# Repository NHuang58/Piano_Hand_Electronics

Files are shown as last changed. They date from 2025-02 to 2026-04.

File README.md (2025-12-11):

# Piano-Hand-API
API using Music 21 and MIDI to convert midi files and piano notes to coordinates for a piano hand.

The KiCAD files have a full PCB design for the barrel jack, LM2896, motor servers, stepper motor driver, and microphone. This includes the Gerber files, drill files, and bill of materials. It also includes the libraries for the symbols and footprints used in this project.

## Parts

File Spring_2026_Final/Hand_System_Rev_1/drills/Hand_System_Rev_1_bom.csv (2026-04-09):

Reference | Qty | Value | DNP | Exclude from BOM | Exclude from Board | Footprint | Datasheet
C1 | 1 | 22u |  |  |  | Capacitor_SMD:C_0805_2012Metric | ~
C2 | 1 | 100 μF |  |  |  | Capacitor_SMD:C_0805_2012Metric | ~
C3,C4 | 2 | 10uF |  |  |  | Capacitor_SMD:C_0805_2012Metric | ~
H1,H2,H3,H4 | 4 | MountingHole |  | Excluded from BOM |  | MountingHole:MountingHole_4.3mm_M4 | ~
J1 | 1 | Barrel_Jack |  |  |  | Connector_BarrelJack:BarrelJack_SwitchcraftConxall_RAPC10U_Horizontal | https://www.sameskydevices.com/product/resource/pj-007.pdf
M1,M2,M3,M4,M5,M6,M8,M9,M10,M11 | 10 | Motor_Servo |  |  |  | Connector_PinHeader_2.54mm:PinHeader_1x03_P2.54mm_Vertical | ~
M7 | 1 | Stepper_Motor |  |  |  | Connector_PinHeader_2.54mm:PinHeader_1x04_P2.54mm_Vertical | ~
Q1,Q3 | 2 | IRLZ44N |  |  |  | Package_TO_SOT_THT:TO-220-3_Vertical | https://www.infineon.com/assets/row/public/documents/24/49/infineon-irlz44n-datasheet-en.pdf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
R1,R14,R28,R35 | 4 | 10k |  |  |  | Resistor_SMD:R_0805_2012Metric | ~
R2,R15 | 2 | 100 |  |  |  | Resistor_SMD:R_0805_2012Metric | ~
R3,R4,R5,R6,R7,R8,R9,R10,R11,R12 | 10 | 1K |  |  |  | Resistor_SMD:R_0805_2012Metric | ~
R13,R16 | 2 | 1k |  |  |  | Resistor_SMD:R_0805_2012Metric | ~
R23,R24,R25,R26,R27,R36,R37,R38,R39,R40 | 10 | 220 |  |  |  | Resistor_SMD:R_0805_2012Metric | ~
U1 | 1 | ESP32-DEVKITC-32UE |  |  |  | DEVKIT_V1_ESP32-WROOM-32:MODULE_DEVKIT_V1_ESP32-WROOM-32
U2,U5,U6 | 3 | LM2596 |  |  |  | PCB_Components:LM2596 | https://www.amazon.com/Seloky-Converter-Adjustable-Electronic-Stabilizer/dp/B0DBVYP91F
U3 | 1 | A4988_Stepper_Motor_Driver |  |  |  | Module:Pololu_Breakout-16_15.2x20.3mm | https://www.pololu.com/product/2980/pictures
U4 | 1 | ~ |  |  |  | Connector_PinHeader_2.54mm:PinHeader_1x04_P2.54mm_Vertical
U7,U8 | 2 | PCA9685PW |  |  |  | Package_SO:TSSOP-28_4.4x9.7mm_P0.65mm | http://www.nxp.com/docs/en/data-sheet/PCA9685.pdf

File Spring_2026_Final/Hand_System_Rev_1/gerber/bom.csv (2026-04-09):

Reference | Qty | Value | DNP | Exclude from BOM | Exclude from Board | Footprint | Datasheet
C1 | 1 | 22u |  |  |  | Capacitor_SMD:C_0805_2012Metric | https://www.mouser.com/ProductDetail/Murata-Electronics/GXT21BR61C226ME13L?qs=d0WKAl%252BL4Kb74FO4906dbA%3D%3D
C2 | 1 | 100 uF |  |  |  | Capacitor_SMD:C_1206_3216Metric | https://www.mouser.com/ProductDetail/Murata-Electronics/GRM31CR61A107MEA8K?qs=hd1VzrDQEGiKPwOlEhCnYw%3D%3D
C3,C4 | 2 | 10uF |  |  |  | Capacitor_SMD:C_0805_2012Metric | https://www.digikey.com/en/products/detail/yageo/CC0805KRX5R7BB106/7164386
H1,H2,H3,H4 | 4 | MountingHole |  | Excluded from BOM |  | MountingHole:MountingHole_4.3mm_M4 | ~
J1 | 1 | Barrel_Jack |  |  |  | Connector_BarrelJack:BarrelJack_SwitchcraftConxall_RAPC10U_Horizontal | https://www.sameskydevices.com/product/resource/pj-007.pdf
M1,M2,M3,M4,M5,M6,M8,M9,M10,M11 | 10 | Motor_Servo |  |  |  | Connector_PinHeader_2.54mm:PinHeader_1x03_P2.54mm_Vertical | ~
M7 | 1 | Stepper_Motor |  |  |  | Connector_PinHeader_2.54mm:PinHeader_1x04_P2.54mm_Vertical | ~
Q1,Q3 | 2 | IRLZ44N |  |  |  | Package_TO_SOT_THT:TO-220-3_Vertical | https://www.infineon.com/assets/row/public/documents/24/49/infineon-irlz44n-datasheet-en.pdf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
R1,R14,R28,R35 | 4 | 10k |  |  |  | Resistor_SMD:R_0805_2012Metric | https://www.digikey.com/en/products/detail/yageo/RC0805FR-0710KL/727535
R2,R15 | 2 | 100 |  |  |  | Resistor_SMD:R_0805_2012Metric | https://www.digikey.com/en/products/detail/yageo/RC0402FR-07100RL/726527
R3,R4,R5,R6,R7,R8,R9,R10,R11,R12 | 10 | 1K |  |  |  | Resistor_SMD:R_0805_2012Metric | https://www.digikey.com/en/products/detail/vishay-dale/CRCW08051K00FKEA/1175637
R13,R16 | 2 | 1k |  |  |  | Resistor_SMD:R_0805_2012Metric | https://www.digikey.com/en/products/detail/vishay-dale/CRCW08051K00FKEA/1175637
R23,R24,R25,R26,R27,R36,R37,R38,R39,R40 | 10 | 220 |  |  |  | Resistor_SMD:R_0805_2012Metric | https://www.digikey.com/en/products/detail/stackpole-electronics-inc/RMCF0805FT220R/1760238
U1 | 1 | ESP32-DEVKITC-32UE |  |  |  | DEVKIT_V1_ESP32-WROOM-32:MODULE_DEVKIT_V1_ESP32-WROOM-32 | ~
U2,U5,U6 | 3 | LM2596 |  |  |  | PCB_Components:LM2596 | https://www.amazon.com/Seloky-Converter-Adjustable-Electronic-Stabilizer/dp/B0DBVYP91F
U3 | 1 | A4988_Stepper_Motor_Driver |  |  |  | Module:Pololu_Breakout-16_15.2x20.3mm | https://www.pololu.com/product/2980/pictures
U4 | 1 | ~ |  |  |  | Connector_PinHeader_2.54mm:PinHeader_1x04_P2.54mm_Vertical | ~
U7,U8 | 2 | PCA9685PW |  |  |  | Package_SO:TSSOP-28_4.4x9.7mm_P0.65mm | http://www.nxp.com/docs/en/data-sheet/PCA9685.pdf

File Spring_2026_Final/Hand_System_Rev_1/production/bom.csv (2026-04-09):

Designator | Footprint | Quantity | Value | LCSC Part #
C1 | 805 | 1 | 22u
C2 | 805 | 1 | 100 μF
J1 | BarrelJack_SwitchcraftConxall_RAPC10U_Horizontal | 1 | Barrel_Jack
M1, M10, M11, M2, M3, M4, M5, M6, M8, M9 | PinHeader_1x03_P2.54mm_Vertical | 10 | Motor_Servo
M7 | PinHeader_1x04_P2.54mm_Vertical | 1 | Stepper_Motor
Q1, Q2 | DirectFET_ST | 2 | IRF6623
R1, R14 | 805 | 2 | 10k
R10, R11, R12, R13, R15, R16, R2, R3, R4, R5, R6, R7, R8, R9 | 805 | 14 | 1K
U1 | MODULE_DEVKIT_V1_ESP32-WROOM-32 | 1 | ESP32-DEVKITC-32UE
U2, U5, U6 | LM2596 | 3 | LM2596
U3 | Pololu_Breakout-16_15.2x20.3mm | 1 | A4988_Stepper_Motor_Driver
U4 | PinHeader_1x04_P2.54mm_Vertical | 1 | ~

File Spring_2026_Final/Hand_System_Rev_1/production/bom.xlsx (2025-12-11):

Comment | Designator | Footprint | LCSC Part #
22u | C1 | 0805 | 1276-1274-2-ND
100 μF | C2 | 0805 | 3372-0805N101J201ADTR-ND
0.1uF | C3 | 0805 | 3372-0805B104K500BDTR-ND
0.47uF | C4 | 0805 | 3372-0805B474K500CCTR-ND
470nF | C5 | 0805 | 3372-0805B474K500CCTR-ND
2.2uF | C6 | 0805 | 3372-0805B225K250CCTR-ND
1uF | C7 | 0805 | 3372-0805N101J201ADTR-ND
Barrel_Jack | J1 | BarrelJack_SwitchcraftConxall_RAPC10U_Horizontal | SC2072-ND
Motor_Servo | M1, M2, M3, M4, M5, M6 | PinHeader_1x03_P2.54mm_Vertical
Stepper_Motor | M7 | PinHeader_1x04_P2.54mm_Vertical
Microphone | MK1 | POM-2244P-C3310-2-R | 668-1415-ND
150k | R1 | 0805 | YAG3409TR-ND
100k | R2 | 0805 | 311-100KARTR-ND
ESP32-DEVKITC-32UE | U1 | MODULE_DEVKIT_V1_ESP32-WROOM-32
LM2596 | U2 | LM2596
A4988_Stepper_Motor_Driver | U3 | Pololu_Breakout-16_15.2x20.3mm
~ | U4 | PinHeader_1x04_P2.54mm_Vertical | `
MAX9814ETD_T | U5 | SON40P300X300X80-15N | MAX9814ETD+TTR-ND
1k | R3,R4, R5,R6,R7,R8 | 0805 | C702831

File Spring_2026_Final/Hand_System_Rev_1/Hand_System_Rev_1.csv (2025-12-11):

Reference | Qty | Value | DNP | Exclude from BOM | Exclude from Board | Footprint | Datasheet
C1 | 1 | 22u |  |  |  | Capacitor_SMD:C_0805_2012Metric | ~
C2 | 1 | 100 μF |  |  |  | Capacitor_SMD:C_0805_2012Metric | ~
C3 | 1 | 0.1uF |  |  |  | Capacitor_SMD:C_0805_2012Metric | ~
C4 | 1 | 0.47uF |  |  |  | Capacitor_SMD:C_0805_2012Metric | ~
C5 | 1 | 470nF |  |  |  | Capacitor_SMD:C_0805_2012Metric | ~
C6 | 1 | 2.2uF |  |  |  | Capacitor_SMD:C_0805_2012Metric | ~
C7 | 1 | 1uF |  |  |  | Capacitor_SMD:C_0805_2012Metric | ~
H1,H2,H3,H4 | 4 | MountingHole |  | Excluded from BOM |  | MountingHole:MountingHole_4.3mm_M4 | ~
J1 | 1 | Barrel_Jack |  |  |  | Connector_BarrelJack:BarrelJack_SwitchcraftConxall_RAPC10U_Horizontal | ~
M1,M2,M3,M4,M5,M6 | 6 | Motor_Servo |  |  |  | Connector_PinHeader_2.54mm:PinHeader_1x03_P2.54mm_Vertical | http://forums.parallax.com/uploads/attachments/46831/74481.png
M7 | 1 | Stepper_Motor |  |  |  | Connector_PinHeader_2.54mm:PinHeader_1x04_P2.54mm_Vertical | http://www.infineon.com/dgdl/Application-Note-TLE8110EE_driving_UniPolarStepperMotor_V1.1.pdf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
MK1 | 1 | Microphone |  |  |  | Sensor_Audio:POM-2244P-C3310-2-R | ~
R1 | 1 | 150k |  |  |  | Resistor_SMD:R_0805_2012Metric | ~
R2 | 1 | 100k |  |  |  | Resistor_SMD:R_0805_2012Metric | ~
R3,R6,R7,R8 | 4 | 1K |  |  |  | Resistor_SMD:R_0805_2012Metric | ~
R4,R5 | 2 | 1k |  |  |  | Resistor_SMD:R_0805_2012Metric | ~
U1 | 1 | ESP32-DEVKITC-32UE |  |  |  | DEVKIT_V1_ESP32-WROOM-32:MODULE_DEVKIT_V1_ESP32-WROOM-32
U2 | 1 | LM2596 |  |  |  | PCB_Components:LM2596
U3 | 1 | A4988_Stepper_Motor_Driver |  |  |  | Module:Pololu_Breakout-16_15.2x20.3mm | https://www.pololu.com/product/2980/pictures
U4 | 1 | ~ |  |  |  | Connector_PinHeader_2.54mm:PinHeader_1x04_P2.54mm_Vertical
U5 | 1 | MAX9814ETD_T |  |  |  | MAX9814ETD_T:SON40P300X300X80-15N

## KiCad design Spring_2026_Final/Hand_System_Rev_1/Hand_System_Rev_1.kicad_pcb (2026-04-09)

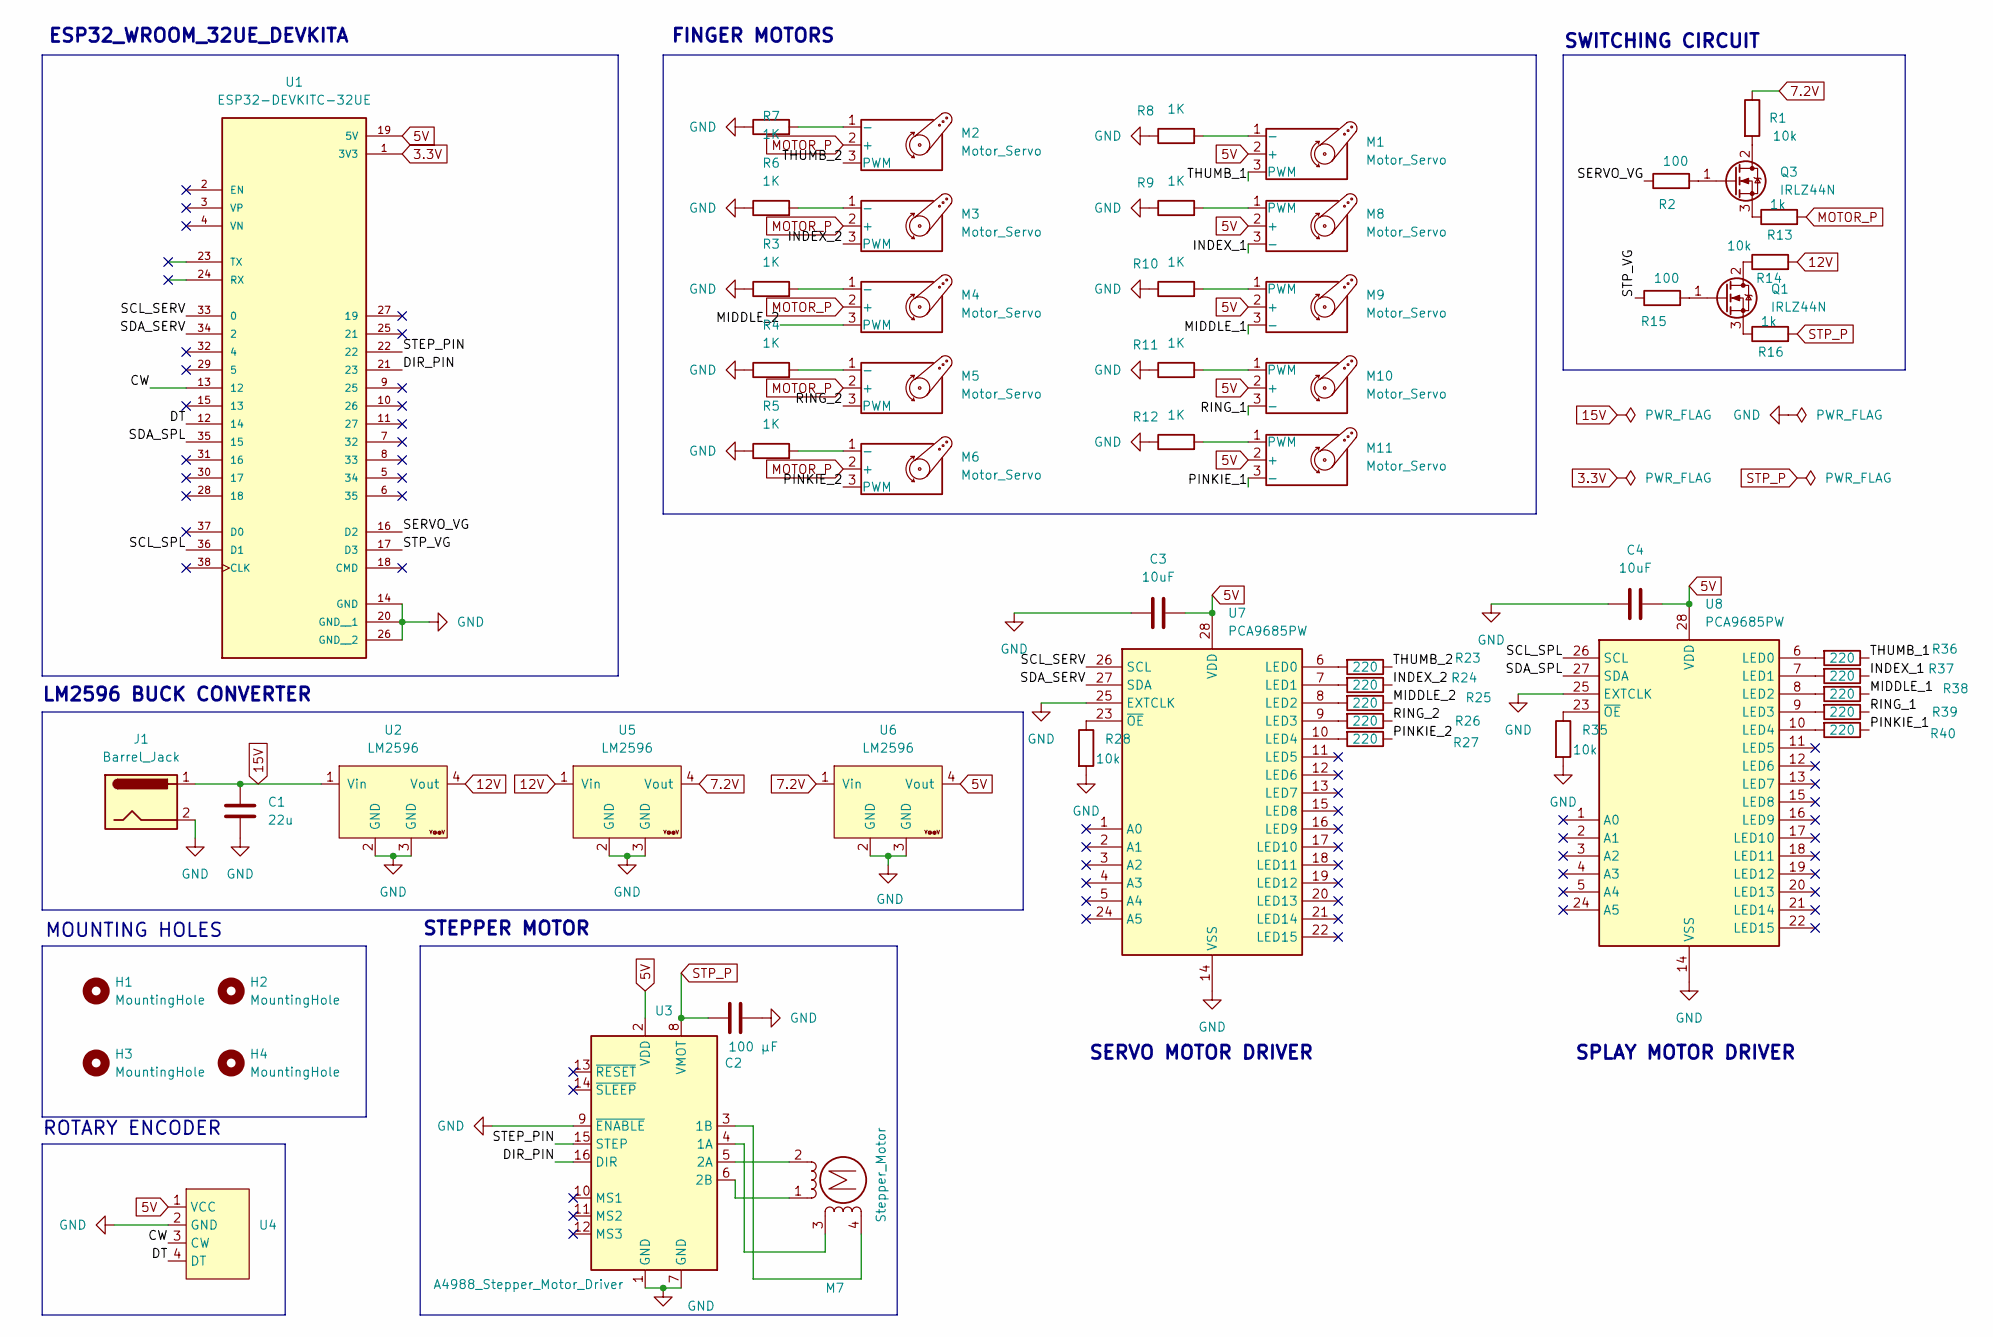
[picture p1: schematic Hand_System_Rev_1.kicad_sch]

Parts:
C1: 22u; C_0805_2012Metric
C2: 100 μF; C_1206_3216Metric
C3, C4: 10uF; C_0805_2012Metric
H1, H2, H3, H4: MountingHole; MountingHole_4.3mm_M4
J1: Barrel_Jack; BarrelJack_SwitchcraftConxall_RAPC10U_Horizontal
M1, M2, M3, M4, M5, M6, M8, M9, M10, M11: Motor_Servo; PinHeader_1x03_P2.54mm_Vertical
M7: Stepper_Motor; PinHeader_1x04_P2.54mm_Vertical
Q1, Q3: IRLZ44N; TO-220-3_Vertical
R1, R14, R28, R35: 10k; R_0805_2012Metric
R2, R15: 100; R_0805_2012Metric
R3, R4, R5, R6, R7, R8, R9, R10, R11, R12: 1K; R_0805_2012Metric
R13, R16: 1k; R_0805_2012Metric
R23, R24, R25, R26, R27, R36, R37, R38, R39, R40: 220; R_0805_2012Metric
U1: ESP32-DEVKITC-32UE; MODULE_DEVKIT_V1_ESP32-WROOM-32; PARTREV V4
U2, U5, U6: LM2596
U3: A4988_Stepper_Motor_Driver; Pololu_Breakout-16_15.2x20.3mm
U4: PinHeader_1x04_P2.54mm_Vertical
U7, U8: PCA9685PW; TSSOP-28_4.4x9.7mm_P0.65mm

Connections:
3.3V: U1.1 (3V3)
5V: C3.2, C4.2, M1.2 (+), M8.2 (+), M9.2 (+), M10.2 (+), M11.2 (+), U1.19 (5V), U3.2 (VDD), U4.1 (VCC), U6.4 (Vout), U7.28 (VDD), U8.28 (VDD)
7.2V: R1.1, U5.4 (Vout), U6.1 (Vin)
12V: R14.2, U2.4 (Vout), U5.1 (Vin)
15V: C1.1, J1.1, U2.1 (Vin)
/CW: U1.13 (12), U4.3 (CW)
/DIR_PIN: U1.21 (23), U3.16 (DIR)
/DT: U1.12 (14), U4.4 (DT)
/INDEX_1: M8.3 (-), R37.1
/INDEX_2: M3.3 (PWM), R24.1
/MIDDLE_1: M9.3 (-), R38.1
/MIDDLE_2: M4.3 (PWM), R25.1
/PINKIE_1: M11.3 (-), R40.1
/PINKIE_2: M6.3 (PWM), R27.1
/RING_1: M10.3 (-), R39.1
/RING_2: M5.3 (PWM), R26.1
/SCL_SERV: U1.33 (0), U7.26 (SCL)
/SCL_SPL: U1.36 (D1), U8.26 (SCL)
/SDA_SERV: U1.34 (2), U7.27 (SDA)
/SDA_SPL: U1.35 (15), U8.27 (SDA)
/SERVO_VG: R2.1, U1.16 (D2)
/STEP_PIN: U1.22, U3.15 (STEP)
/STP_VG: R15.1, U1.17 (D3)
/THUMB_1: M1.3 (PWM), R36.1
/THUMB_2: M2.3 (PWM), R23.1
GND: C1.2, C2.2, C3.1, C4.1, J1.2, R3.1, R4.1, R5.1, R6.1, R7.1, R8.1, R9.1, R10.1, R11.1, R12.1, R28.2, R35.2, U1.14 (GND), U1.20 (GND__1), U1.26 (GND__2), U2.2 (GND), U2.3 (GND), U3.1 (GND), U3.7 (GND), U3.9 (~ENABLE), U4.2 (GND), U5.2 (GND), U5.3 (GND), U6.2 (GND), U6.3 (GND), U7.14 (VSS), U7.25 (EXTCLK), U8.14 (VSS), U8.25 (EXTCLK)
MOTOR_P: M2.2 (+), M3.2 (+), M4.2 (+), M5.2 (+), M6.2 (+), R13.2
unnamed: M1.1 (-), R8.2
unnamed: M2.1 (-), R7.2
unnamed: M3.1 (-), R6.2
unnamed: M4.1 (-), R3.2
unnamed: M5.1 (-), R4.2
unnamed: M6.1 (-), R5.2
unnamed: M7.2 (-), U3.5 (2A)
unnamed: M8.1 (PWM), R9.2
unnamed: M9.1 (PWM), R10.2
unnamed: M10.1 (PWM), R11.2
unnamed: M11.1 (PWM), R12.2
unnamed: Q1.2 (D), R14.1
unnamed: Q1.1 (G), R15.2
unnamed: Q1.3 (S), R16.1
unnamed: Q3.2 (D), R1.2
unnamed: Q3.1 (G), R2.2
unnamed: Q3.3 (S), R13.1
unnamed: M7.3, U3.4 (1A)
unnamed: M7.4, U3.3 (1B)
unnamed: M7.1, U3.6 (2B)
unnamed: R23.2, U7.6 (LED0)
unnamed: R24.2, U7.7 (LED1)
unnamed: R25.2, U7.8 (LED2)
unnamed: R26.2, U7.9 (LED3)
unnamed: R27.2, U7.10 (LED4)
unnamed: R28.1, U7.23 (~OE)
unnamed: R36.2, U8.6 (LED0)
unnamed: R37.2, U8.7 (LED1)
unnamed: R38.2, U8.8 (LED2)
unnamed: R39.2, U8.9 (LED3)
unnamed: R40.2, U8.10 (LED4)
unnamed: R35.1, U8.23 (~OE)
STP_P: C2.1, R16.2, U3.8 (VMOT)

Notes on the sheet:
ROTARY ENCODER
FINGER MOTORS
LM2596 BUCK CONVERTER
SPLAY MOTOR DRIVER
STEPPER MOTOR
MOUNTING HOLES
SWITCHING CIRCUIT
ESP32_WROOM_32UE_DEVKITA
SERVO MOTOR DRIVER

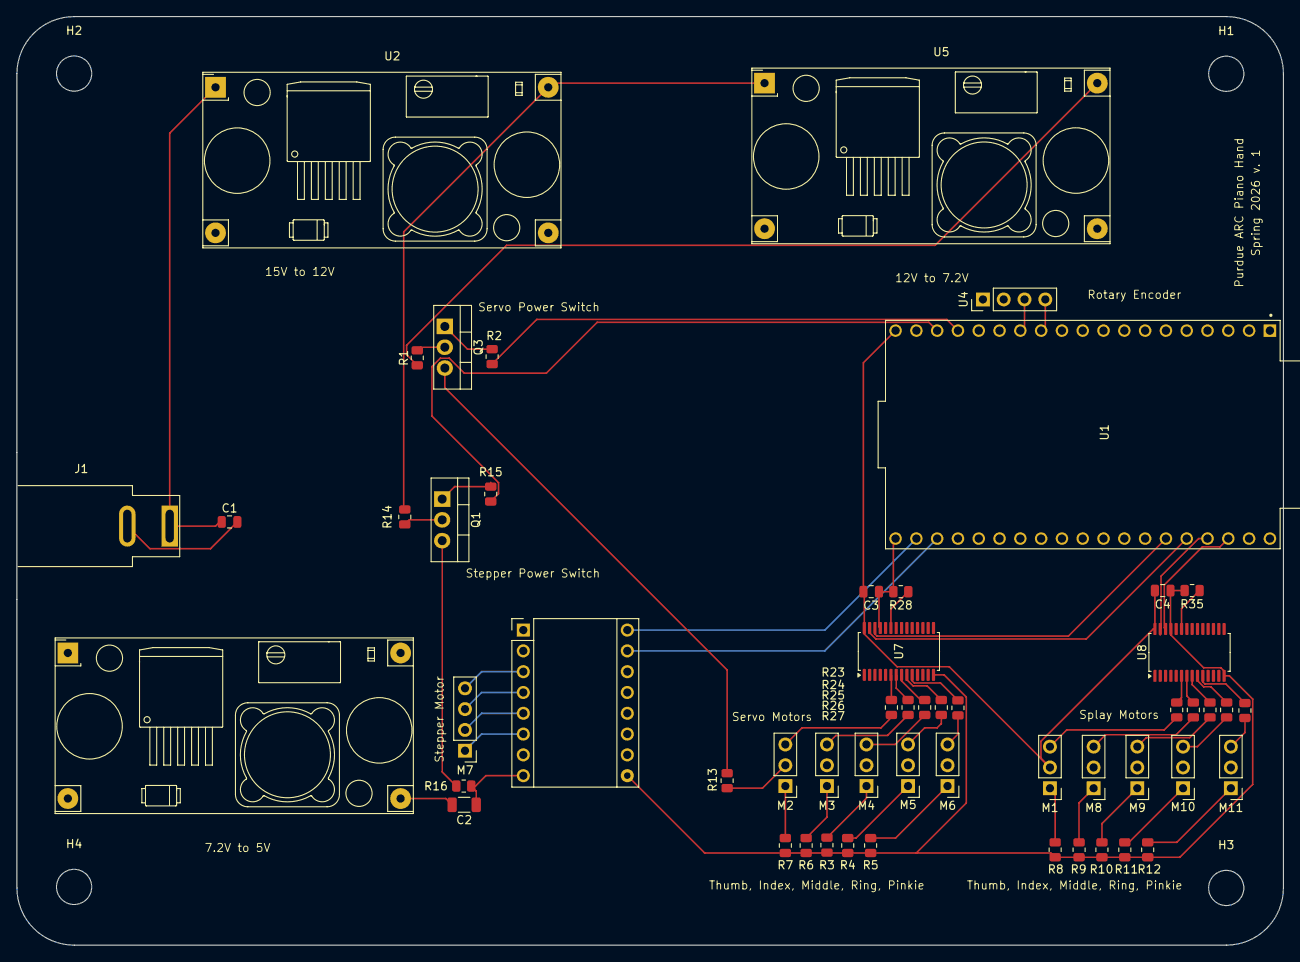
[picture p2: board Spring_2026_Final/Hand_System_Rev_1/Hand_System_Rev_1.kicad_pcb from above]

Board: 4 copper layers, 154.7 x 113.4 mm, 58 parts (0 on the bottom side), 59 nets.

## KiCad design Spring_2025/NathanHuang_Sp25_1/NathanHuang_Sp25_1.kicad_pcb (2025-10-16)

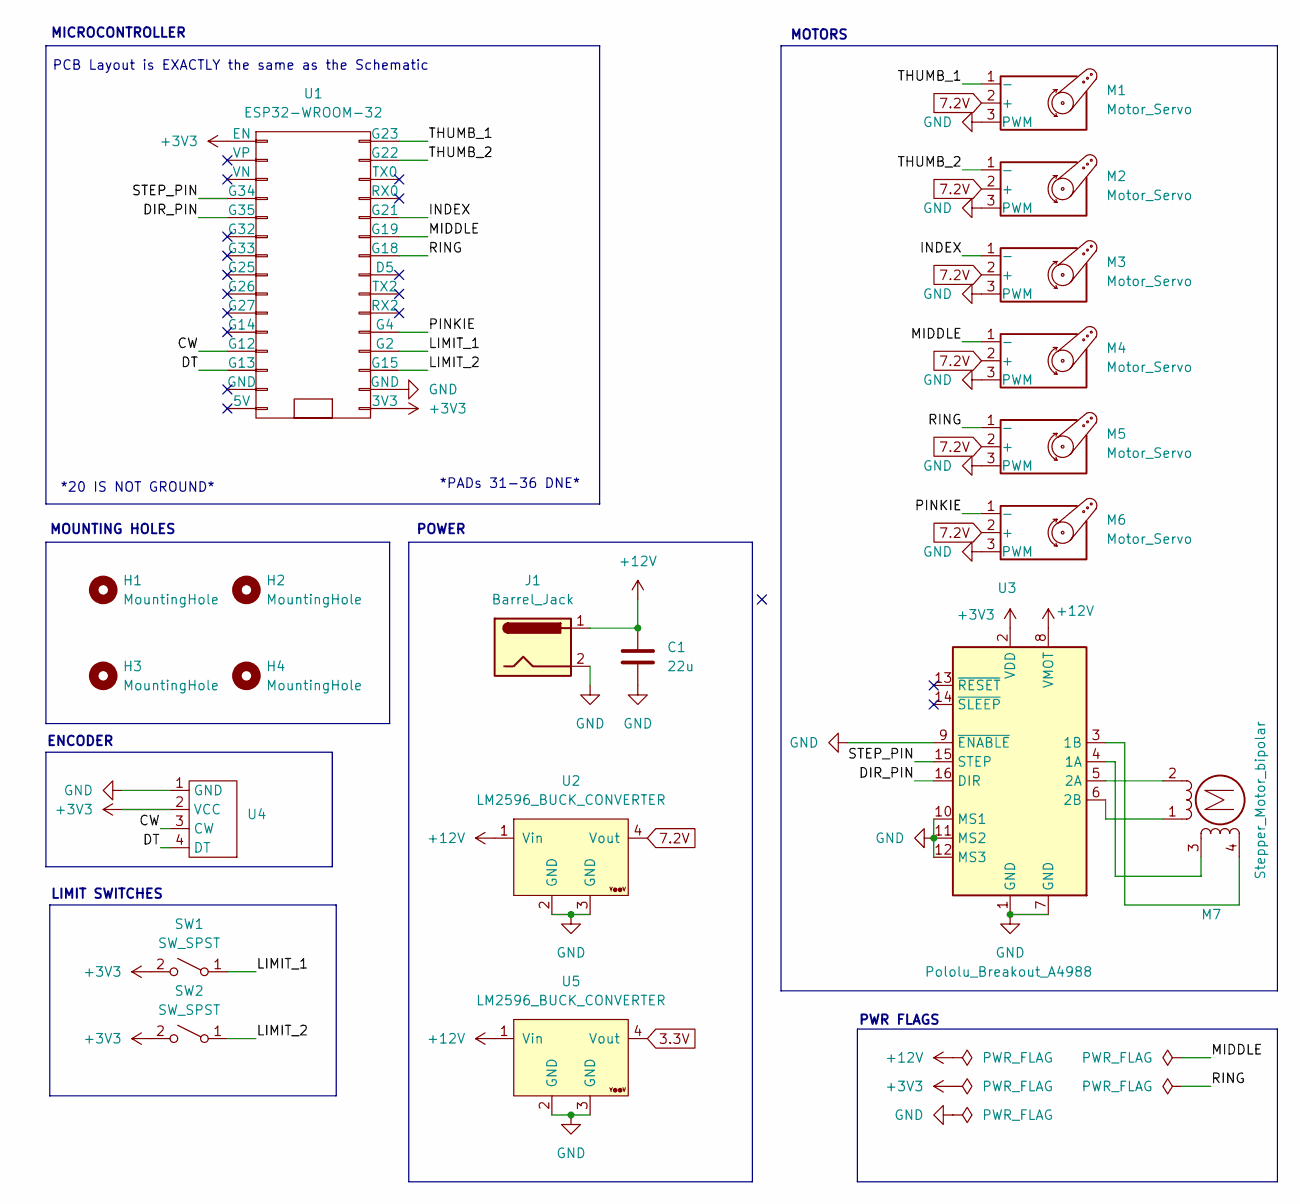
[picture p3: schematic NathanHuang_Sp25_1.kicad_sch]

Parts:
C1: 22u; CP_Radial_D4.0mm_P1.50mm
H1, H2, H3, H4: MountingHole; MountingHole_5.3mm_M5
J1: Barrel_Jack; BarrelJack_SwitchcraftConxall_RAPC10U_Horizontal
M1, M2, M3, M4, M5, M6: Motor_Servo; PinHeader_1x03_P2.54mm_Vertical
M7: Stepper_Motor_bipolar; PinHeader_1x04_P2.54mm_Vertical
SW1, SW2: SW_SPST; PinHeader_1x02_P2.54mm_Vertical
U1: ESP32-WROOM-32
U2, U5: LM2596_BUCK_CONVERTER
U3: Pololu_Breakout_A4988; Pololu_Breakout-16_15.2x20.3mm
U4: PinHeader_1x04_P2.54mm_Vertical

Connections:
7.2V: M1.2 (+), M2.2 (+), M3.2 (+), M4.2 (+), M5.2 (+), M6.2 (+), U2.4 (Vout)
+3V3: SW1.2 (B), SW2.2 (B), U1.1 (EN), U1.30 (3V3), U3.2 (VDD), U4.2 (VCC)
+12V: C1.1, J1.1, U2.1 (Vin), U3.8 (VMOT), U5.1 (Vin)
/CW: U1.12 (G12), U4.3 (CW)
/DIR_PIN: U1.5 (G35), U3.16 (DIR)
/DT: U1.13 (G13), U4.4 (DT)
/INDEX: M3.1 (-), U1.20 (G21)
/LIMIT_1: SW1.1 (A), U1.27 (G2)
/LIMIT_2: SW2.1 (A), U1.28 (G15)
/MIDDLE: M4.1 (-), U1.21 (G19)
/PINKIE: M6.1 (-), U1.26 (G4)
/RING: M5.1 (-), U1.22 (G18)
/STEP_PIN: U1.4 (G34), U3.15 (STEP)
/THUMB_1: M1.1 (-), U1.16 (G23)
/THUMB_2: M2.1 (-), U1.17 (G22)
GND: C1.2, J1.2, M1.3 (PWM), M2.3 (PWM), M3.3 (PWM), M4.3 (PWM), M5.3 (PWM), M6.3 (PWM), U1.29 (GND), U2.2 (GND), U2.3 (GND), U3.1 (GND), U3.7 (GND), U3.9 (~ENABLE), U3.10 (MS1), U3.11 (MS2), U3.12 (MS3), U4.1 (GND), U5.2 (GND), U5.3 (GND)
unnamed: M7.2 (-), U3.5 (2A)
unnamed: M7.3, U3.4 (1A)
unnamed: M7.4, U3.3 (1B)
unnamed: M7.1, U3.6 (2B)

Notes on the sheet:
MOTORS
MICROCONTROLLER
ENCODER
PWR FLAGS
POWER
LIMIT SWITCHES
PCB Layout is EXACTLY the same as the Schematic
*20 IS NOT GROUND*
MOUNTING HOLES
*PADs 31-36 DNE*

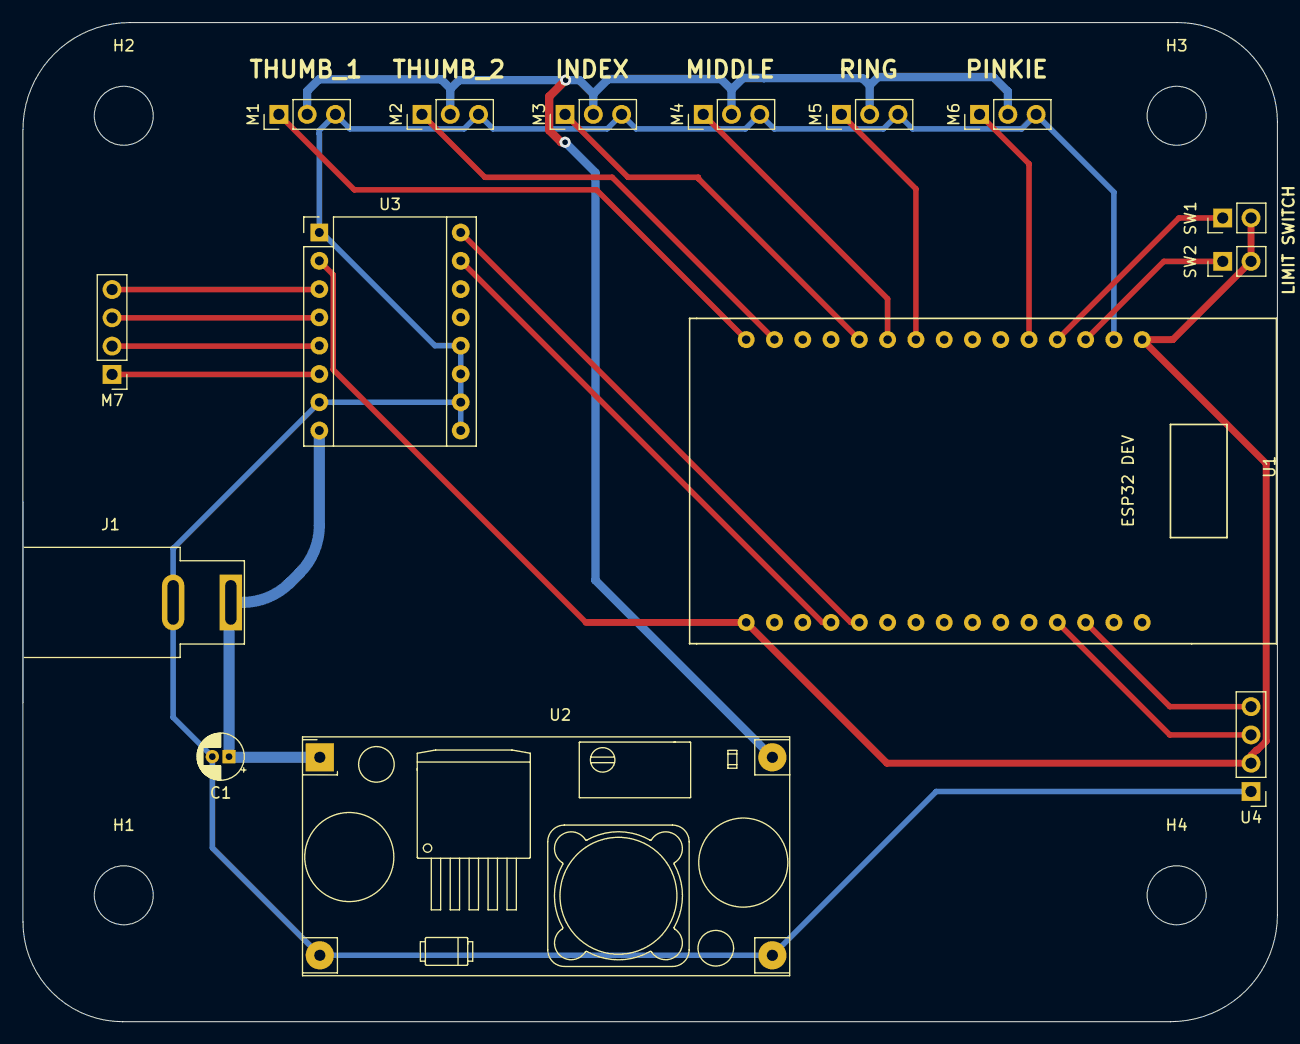
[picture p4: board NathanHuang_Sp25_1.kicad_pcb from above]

Board: 2 copper layers, 112.7 x 89.7 mm, 19 parts (0 on the bottom side), 20 nets.

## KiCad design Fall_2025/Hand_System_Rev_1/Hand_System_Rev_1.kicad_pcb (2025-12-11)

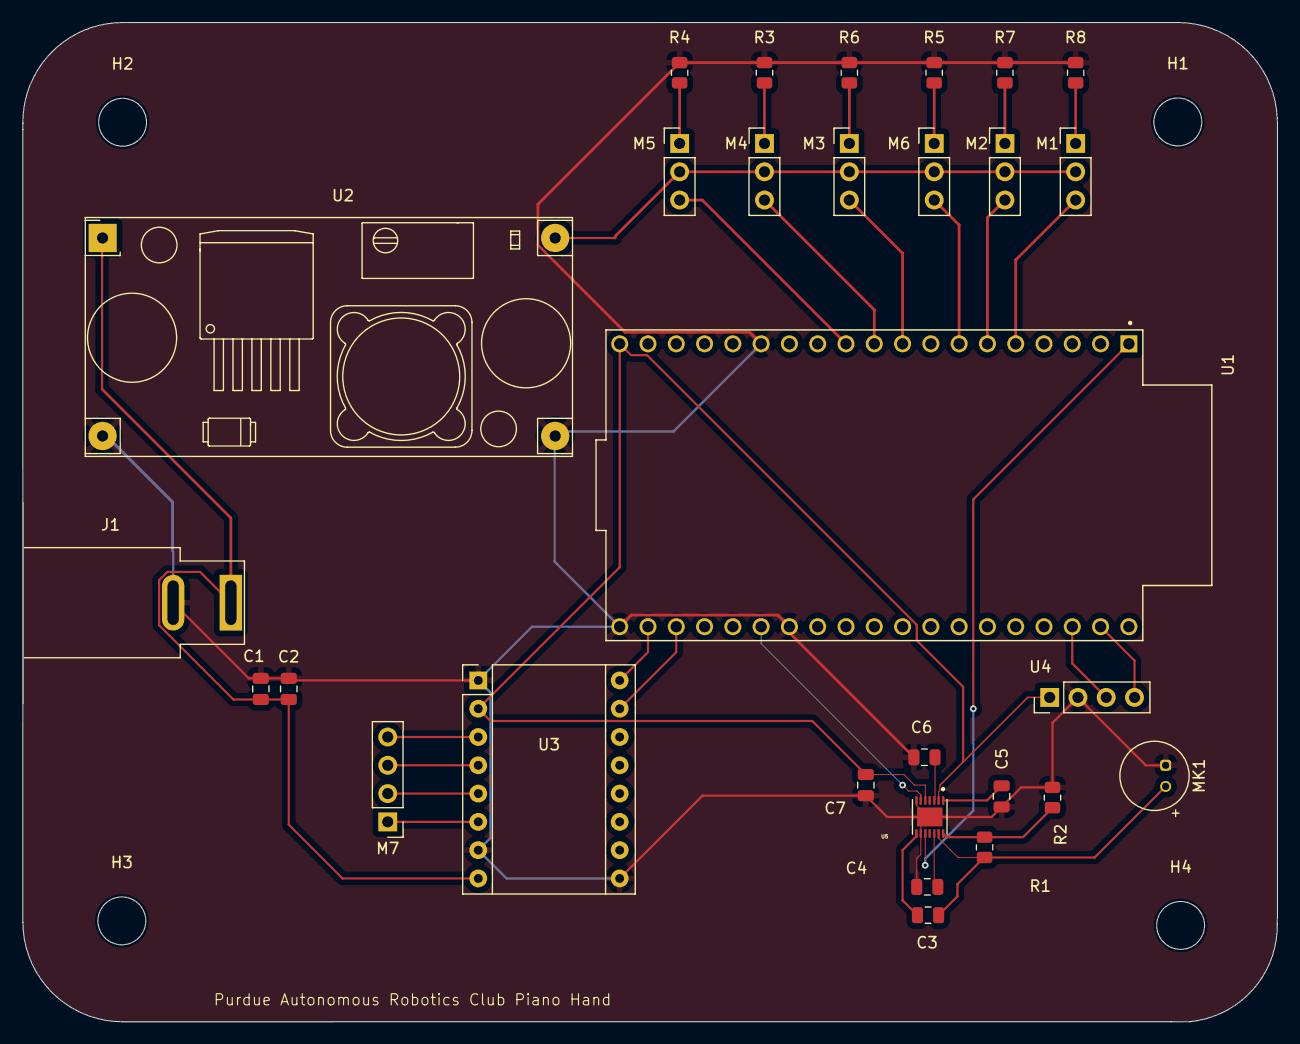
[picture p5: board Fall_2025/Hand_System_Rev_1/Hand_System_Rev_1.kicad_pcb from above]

Board: 2 copper layers, 112.7 x 89.7 mm, 33 parts (0 on the bottom side), 32 nets.

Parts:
C1: 22u; C_0805_2012Metric
C2: 100 μF; C_0805_2012Metric
C3: 0.1uF; C_0805_2012Metric
C4: 0.47uF; C_0805_2012Metric
C5: 470nF; C_0805_2012Metric
C6: 2.2uF; C_0805_2012Metric
C7: 1uF; C_0805_2012Metric
H1, H2, H3, H4: MountingHole; MountingHole_4.3mm_M4
J1: Barrel_Jack; BarrelJack_SwitchcraftConxall_RAPC10U_Horizontal
M1, M2, M3, M4, M5, M6: Motor_Servo; PinHeader_1x03_P2.54mm_Vertical
M7: Stepper_Motor; PinHeader_1x04_P2.54mm_Vertical
MK1: Microphone; POM-2244P-C3310-2-R
R1: 150k; R_0805_2012Metric
R2: 100k; R_0805_2012Metric
R3, R4, R5, R6, R7, R8: 1K; R_0805_2012Metric
U1: ESP32-DEVKITC-32UE; MODULE_DEVKIT_V1_ESP32-WROOM-32
U2: LM2596
U3: A4988_Stepper_Motor_Driver; Pololu_Breakout-16_15.2x20.3mm
U4: PinHeader_1x04_P2.54mm_Vertical
U5: MAX9814ETD_T; SON40P300X300X80-15N

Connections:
3.3V: U1.1 (3V3), U5.10 (GAIN)
5V: C7.1, U1.19 (5V), U3.2 (VDD), U4.1 (VCC), U5.2 (~SHDN), U5.5 (VDD)
7.2V: M1.2 (+), M2.2 (+), M3.2 (+), M4.2 (+), M5.2 (+), M6.2 (+), U2.4 (Vout)
12V: C1.1, C2.1, J1.1, U2.1 (Vin), U3.8 (VMOT)
/CW: U1.36 (D1), U4.3 (CW)
/DIR_PIN: U1.21 (23), U3.16 (DIR)
/DT: U1.37 (D0), U4.4 (DT)
/INDEX: M3.3 (PWM), U1.9 (25)
/MIDDLE: M4.3 (PWM), U1.10 (26)
/MP_OUT: U1.25 (21), U5.6 (MICOUT)
/PINKIE: M6.3 (PWM), U1.7 (32)
/RING: M5.3 (PWM), U1.11 (27)
/STEP_PIN: U1.22, U3.15 (STEP)
/THUMB_1: M1.3 (PWM), U1.5 (34)
/THUMB_2: M2.3 (PWM), U1.6 (35)
GND: C1.2, C2.2, C4.1, C5.1, C6.1, C7.2, J1.2, MK1.1 (-), R2.2, R3.1, R4.1, R5.1, R6.1, R7.1, R8.1, U1.14 (GND), U1.20 (GND__1), U1.26 (GND__2), U2.2 (GND), U2.3 (GND), U3.1 (GND), U3.7 (GND), U3.9 (~ENABLE), U4.2 (GND), U5.7 (GND), U5.9 (A/R), U5.15 (EP)
unnamed: M1.1 (-), R8.2
unnamed: M2.1 (-), R7.2
unnamed: M3.1 (-), R6.2
unnamed: M4.1 (-), R3.2
unnamed: M5.1 (-), R4.2
unnamed: M6.1 (-), R5.2
unnamed: M7.2 (-), U3.5 (2A)
unnamed: C3.1, MK1.2 (+), R1.1, U5.13 (MICBIAS)
unnamed: M7.3, U3.4 (1A)
unnamed: M7.4, U3.3 (1B)
unnamed: M7.1, U3.6 (2B)
unnamed: C4.2, U5.12 (BIAS)
unnamed: C6.2, U5.3 (CG)
unnamed: C5.2, U5.1 (CT)
unnamed: C3.2, U5.8 (MICIN)
unnamed: R1.2, R2.1, U5.14 (TH)

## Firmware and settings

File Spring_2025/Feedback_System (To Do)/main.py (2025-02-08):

import machine
import time
from stepper import *

finger_distances = [0, 0, 0, 0, 0] #FIX TO FIND THE DISTANCE BETWEEN FINGERS (NOT CONSTANT)

def main():
    while True:
        # Get the position of the stepper motor
        position = getPosition()
        # Fix the position of the stepper motor
        fixPosition()
        # Sleep for 1 second
        time.sleep(1)

if __name__ == "__main__":
    main()

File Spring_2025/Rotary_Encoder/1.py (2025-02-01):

from machine import Pin
import time

# Pin definitions
CLK_PIN = 25  # GPIO25 connected to the rotary encoder's CLK pin
DT_PIN = 26   # GPIO26 connected to the rotary encoder's DT pin

# Constants
DIRECTION_CW = 0   # Clockwise direction
DIRECTION_CCW = 1  # Counter-clockwise direction
STEPS_PER_REVOLUTION = 600  # Number of steps for one full rotation (360°)

# Variables
counter = 0
direction = DIRECTION_CW
prev_CLK_state = 0

# Initialize pins
clk = Pin(CLK_PIN, Pin.IN, Pin.PULL_UP)
dt = Pin(DT_PIN, Pin.IN, Pin.PULL_UP)


duration = 0
# Main loop
while True:
    # Read the current state of the CLK pin
    CLK_state = clk.value()

    # Check if the CLK pin state has changed
    if CLK_state != prev_CLK_state:
        # If the state of CLK is HIGH, a pulse occurred
        if CLK_state == 1:
            # Read the DT pin to determine the direction
            if dt.value() == 1:
                counter -= 1
                direction = DIRECTION_CCW
            else:
                counter += 1
                direction = DIRECTION_CW

            # Calculate degrees
            degrees = (counter % STEPS_PER_REVOLUTION) * (360 / STEPS_PER_REVOLUTION)
            print("Rotary Encoder:: direction:", "CLOCKWISE" if direction == DIRECTION_CW else "ANTICLOCKWISE", "- count:", counter, "- degrees:", degrees)

        # Save the current CLK state for the next iteration
        prev_CLK_state = CLK_state

    # Small delay to reduce CPU usage
    duration += 1
    time.sleep_ms(1000)
    if (duration == 15):
        print("Program ended")
        break

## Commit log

2025-02-01 Create encoder
2025-02-01 Rotary Encoder
2025-03-01 Version 3 PCB
    [Version 3.kicad_pcb, Version 3.kicad_sch]
2025-03-01 Added Footprints
2025-03-07 Schematic Changes
    [NathanHuang_Sp25_1.kicad_pcb, NathanHuang_Sp25_1.kicad_sch, Version 3.kicad_pcb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]
2025-03-08 footprint added
    for stepper motor driver
2025-03-08 Schematic Done
    [NathanHuang_Sp25_1.kicad_pcb, NathanHuang_Sp25_1.kicad_sch]
2025-03-08 Routed PCB
    [NathanHuang_Sp25_1.kicad_pcb]
2025-03-08 PCB Changes
    [NathanHuang_Sp25_1.kicad_pcb, NathanHuang_Sp25_1.kicad_sch]
2025-03-09 Finished PCB, Ready for Print
    [NathanHuang_Sp25_1.kicad_pcb, NathanHuang_Sp25_1.kicad_sch]
2025-03-29 PCB Updates
    [NathanHuang_Sp25_1.kicad_pcb, NathanHuang_Sp25_1.kicad_sch]
2025-04-05 4/4 Changes
    [NathanHuang_Sp25_1.kicad_pcb, NathanHuang_Sp25_1.kicad_sch]
2025-04-05 Found Footprint
    New to find new schematic for 30 pin
    [NathanHuang_Sp25_1.kicad_pcb, NathanHuang_Sp25_1.kicad_sch]
2025-04-11 Overwrite Changes
    [NathanHuang_Sp25_1.kicad_pcb, NathanHuang_Sp25_1.kicad_sch]
2025-04-12 Don't clone
    [NathanHuang_Sp25_1.kicad_pcb, NathanHuang_Sp25_1.kicad_sch]
2025-04-12 Updated PCB schematic
    [NathanHuang_Sp25_1.kicad_sch]
2025-04-19 Gerbers ready
    [NathanHuang_Sp25_1.kicad_pcb]
2025-04-19 PCB V4 Done
    [NathanHuang_Sp25_1-B_Cu.gbr, NathanHuang_Sp25_1-B_Mask.gbr, NathanHuang_Sp25_1-B_Paste.gbr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]
2025-04-26 Gerber Files
2025-10-16 Added files for MAX 9814
    [MAX9814ETD_T.step]
2025-10-16 Found footprints
2025-10-16 Updated MAX9814
    [MAX9814ETD_T.step]
2025-10-16 Updated files for esp32 devkitc
2025-10-16 10-16-25 Changes
    [Hand_System_Rev_1.kicad_pcb, Hand_System_Rev_1.kicad_sch]
2025-11-02 added microphone
    [Hand_System_Rev_1.kicad_sch]
2025-11-03 creating kicad pcb schematic
    [Hand_System_Rev_1.kicad_pcb, Hand_System_Rev_1.kicad_sch]
2025-12-11 Finalized the pcb design
    Included microphone and other modules.
    Successfully got gerber files, drill files, and bom
    [Hand_System_Rev_1-B_Cu.gbl, Hand_System_Rev_1-B_Mask.gbs, Hand_System_Rev_1-B_Paste.gbp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]
2025-12-11 Update README with KiCAD and PCB design information
    Added details about KiCAD files and PCB design.
2026-02-21 update electrical schematic to include 10 servo motors, two buck converteds, and removed microphone
    [555timer.kicad_pcb, 555timer.kicad_sch, Hand_System_Rev_1.kicad_sch]
2026-02-22 added more stuff for switching circuitry
    [Hand_System_Rev_1.kicad_sch]
2026-03-04 added more stuff
    [Hand_System_Rev_1.kicad_pcb, Hand_System_Rev_1.kicad_sch]
2026-03-04 new project in spring 2026
    [555timer.kicad_pcb, 555timer.kicad_sch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]
2026-03-04 more stuff for organizing into spring 2026
    [Hand_System_Rev_1.kicad_pcb]
2026-03-07 Finished pcb design spring 2026
    [Hand_System_Rev_1-B_Cu.gbr, Hand_System_Rev_1-B_Mask.gbr, Hand_System_Rev_1-B_Paste.gbr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]
2026-04-09 finish pcb design
    [Hand_System_Rev_1-B_Cu.gbr, Hand_System_Rev_1-B_Mask.gbr, Hand_System_Rev_1-B_Paste.gbr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]
